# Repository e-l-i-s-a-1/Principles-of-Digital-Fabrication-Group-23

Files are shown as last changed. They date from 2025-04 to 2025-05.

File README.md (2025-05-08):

# Principles-of-Digital-Fabrication
## Group 23
### Violent light-chasing alarm clock

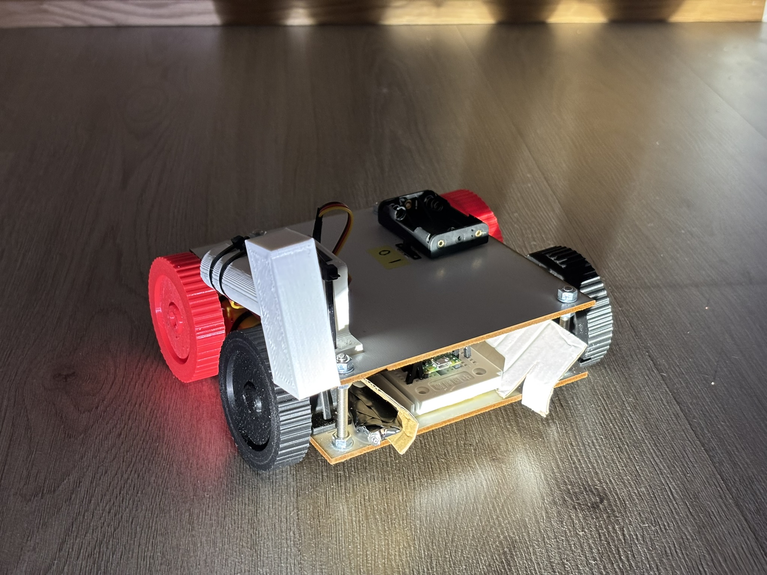
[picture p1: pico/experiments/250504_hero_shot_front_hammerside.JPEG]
Violent light-chasing alarm clock


---

### Contents of the repository:

```
cad:
    -stl-files of the 3D-printed components

pico:
    dev:
        -collection of Python-scripts tested with Pico (including the final "main_final.py")
        -final code with some comments as a .png
        -micropython firmware for Pico (.uf2)
        -schematic as a pptx- and jpeg-file
  
    docs:
        -documentations and datasheets of the used components
  
    experiments:
        -pictures and videos of the design/building process and testing

sketches:
    -some sketches and ideation from early phase of the design

-materials.xlsx (the materials & components list including costs and specifications)

-README.md (this file)
```

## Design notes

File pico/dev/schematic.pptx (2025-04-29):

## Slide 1

Battery holder (3 x AAA)

8 male-female jumpers
4 male-male jumper

ON

Switch

OFF

+

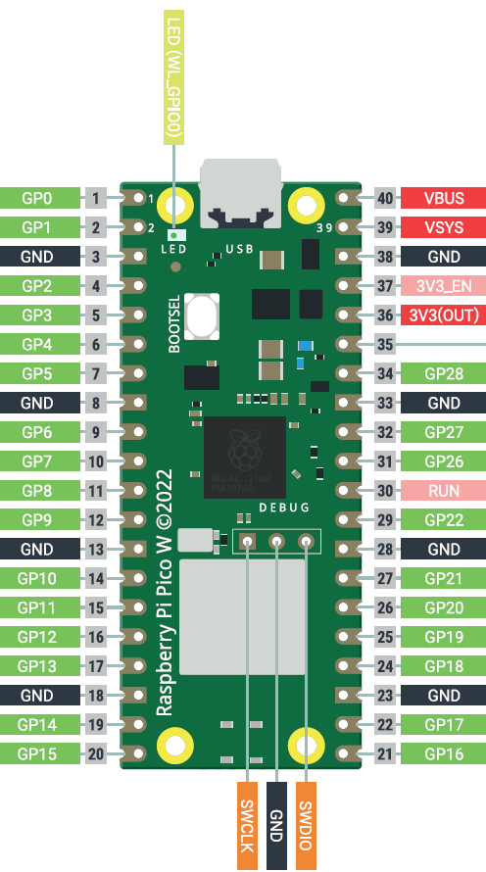
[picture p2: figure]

Big breadboard +

+

Big breadboard -

Schottky diode

C

C

Phototransistor L

E

E

Motor R signal

Phototransistor R

10kΩ resistor

Motor L signal

10kΩ resistor

Servo signal

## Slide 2

Motor R

+

Big breadboard +

Servo

PWM

+

Big breadboard -

Motor R signal

Big breadboard +

O4

L293D H-bridge

VSS

I4

G

G

O3

I3

E2

Big breadboard -

Big breadboard +

Servo signal

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
Motor L signal

3 male-male jumpers

Big breadboard +

Big breadboard -

Big breadboard +

Motor L

+

12 male-male jumpers

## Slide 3

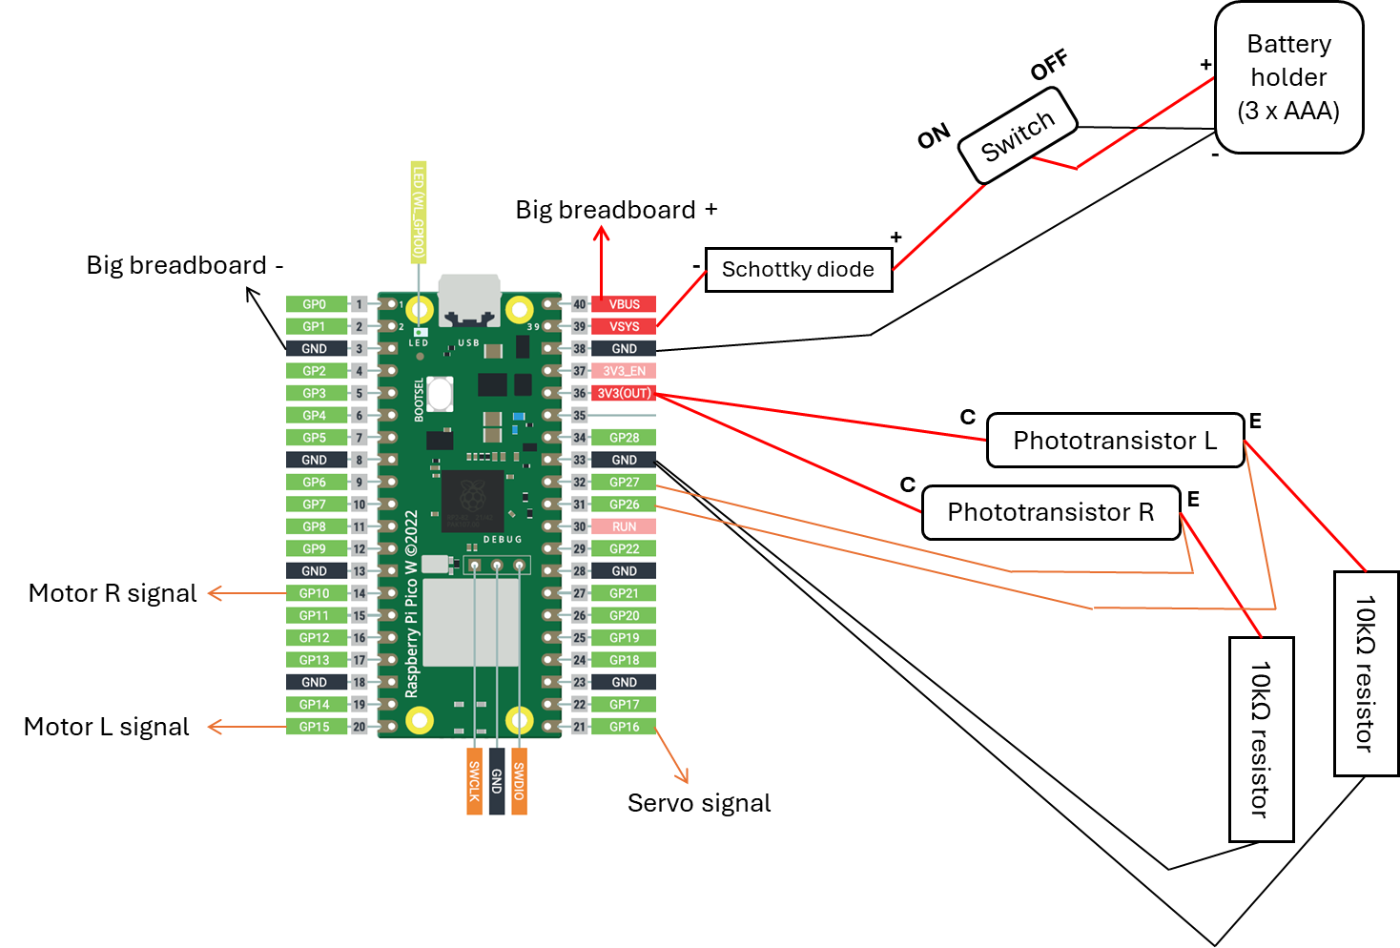
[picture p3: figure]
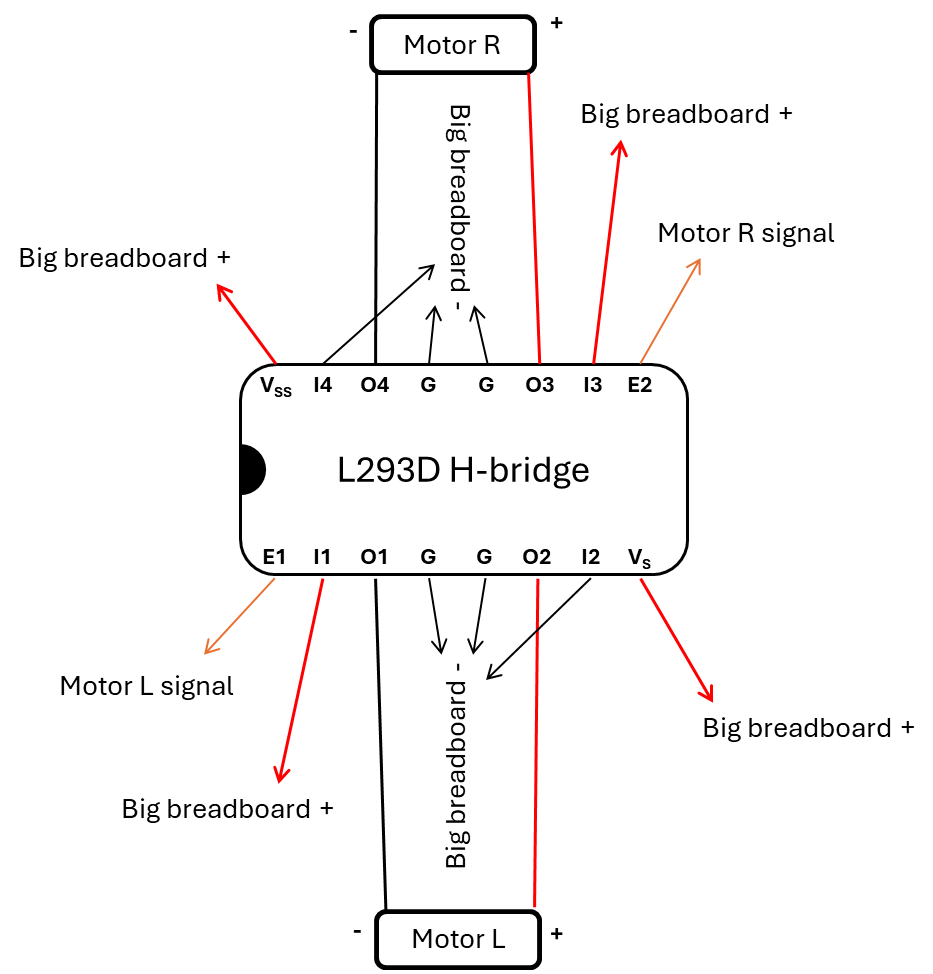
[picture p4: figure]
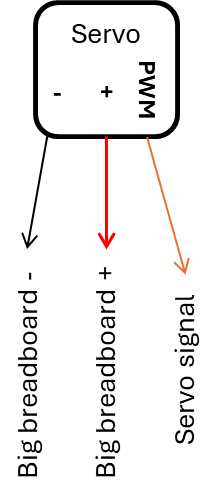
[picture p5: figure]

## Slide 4

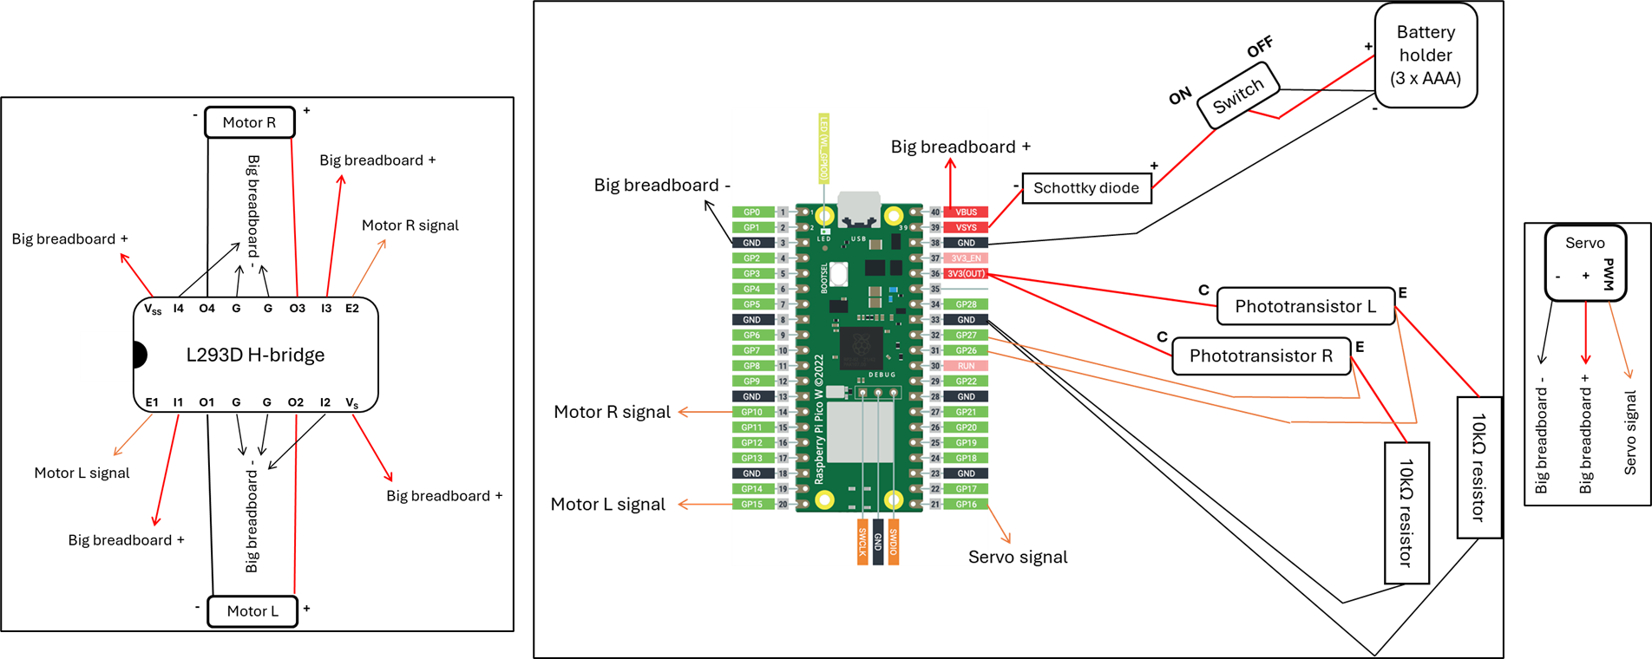
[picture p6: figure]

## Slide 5

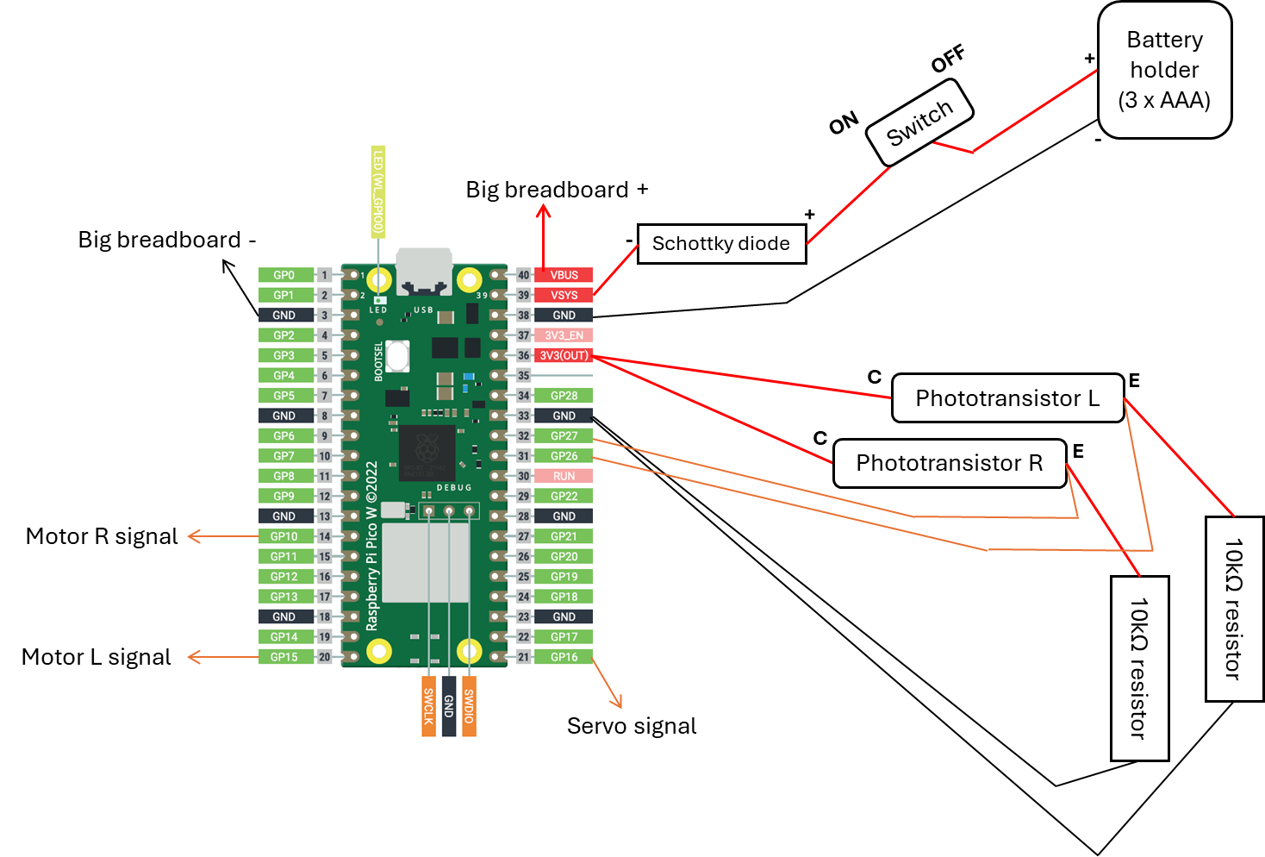
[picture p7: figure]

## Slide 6

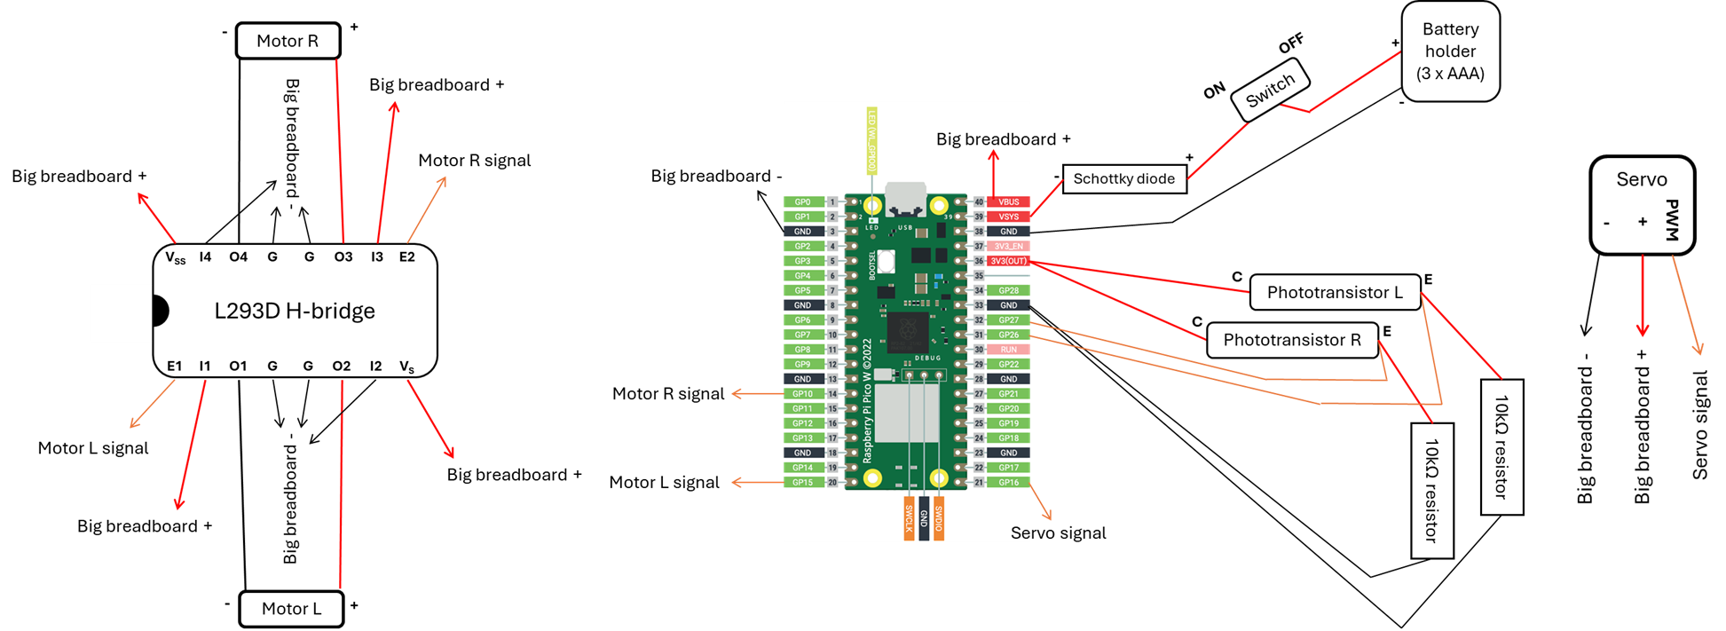
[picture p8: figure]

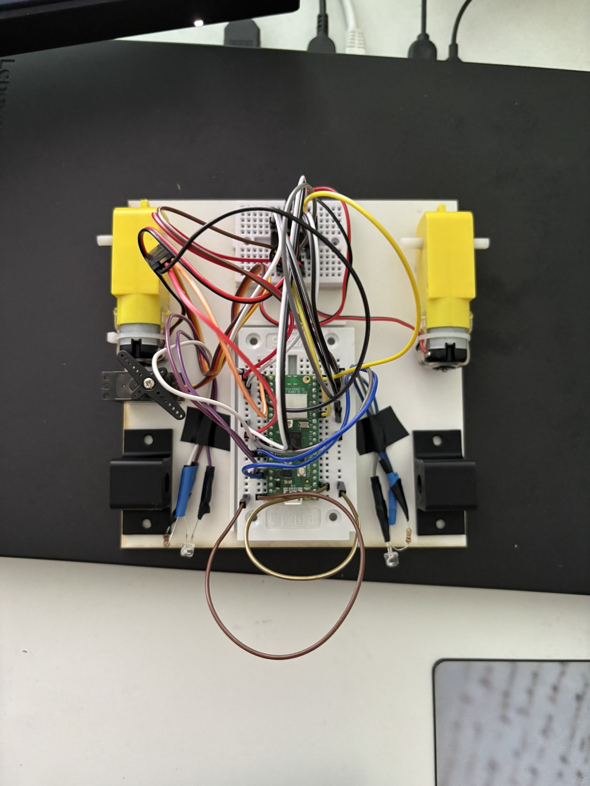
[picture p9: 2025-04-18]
pico/experiments/250417_electronics_topview.JPEG

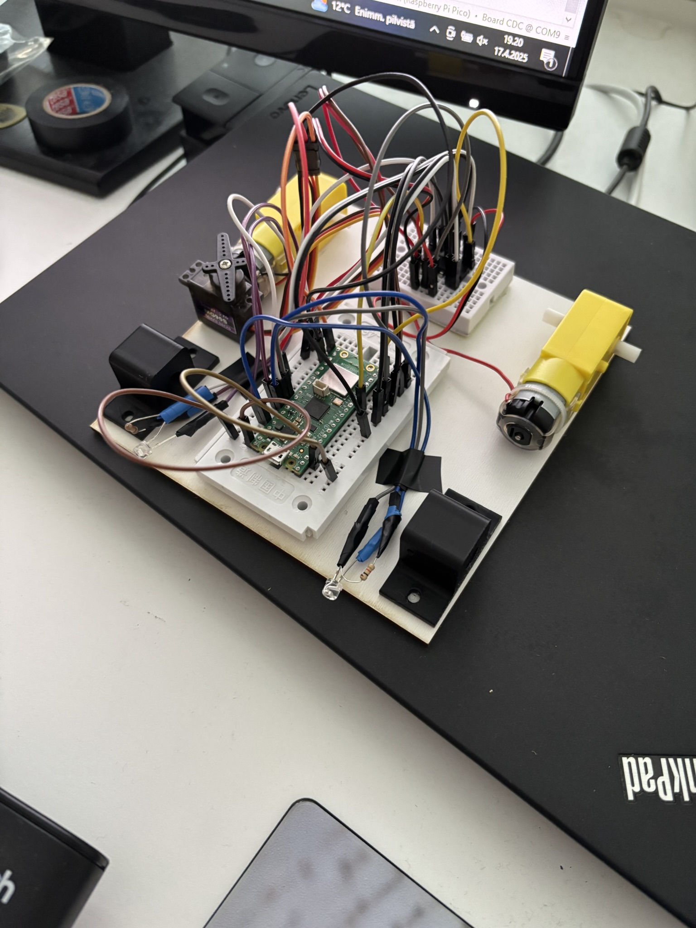
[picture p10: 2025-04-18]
pico/experiments/250417_electronics.JPEG

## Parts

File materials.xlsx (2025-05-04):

Materials
Group 23
violent light-chasing alarm clock |  |  | Updated: | 250503
# | Item | Size (in materials) | Quantity | Material / component specification | Cost per unit [€] | Unit | Total [€]
1 | Frame plate v1 | 135 x 65 x 3 mm | 4 | Plywood (thickness = 3 mm) | 2.1e-05 | mm2 | 0.7371
2 | Frame plate v2 | 150 x 145 x 3 mm | 2 | Plywood (thickness = 3 mm) | 2.1e-05 | mm2 | 0.9135
3 | Front wheel | 35931.574 mm3 / 28 g | 2 | PLA | 0.014 | g | 0.784
4 | Front wheel bracket v1 | 9213.417 mm3 / 9 g | 1 | PLA | 0.014 | g | 0.126
5 | Front wheel bracket v2 | 9002.649 mm3 / 9 g | 2 | PLA | 0.014 | g | 0.252
6 | Microcontroller |  | 1 | Raspberry Pi Pico W | 8.11 | piece | 8.11
7 | Breadboard |  | 1 | Big | 5.35 | piece | 5.35
8 | Breadboard |  | 1 | Small | 2.72 | piece | 2.72
9 | Phototransistor |  | 2 | TEPT5700 | 0.46 | piece | 0.92
10 | Resistor |  | 2 | 10k ohm | 0.24 | piece | 0.48
11 | Gear motor |  | 2 | GEARMOTOR 200 RPM 3-6V DC (Adafruit 3777) | 2.72 | piece | 5.44
12 | H-bridge |  | 1 | L293D | 7.24 | piece | 7.24
13 | Microservo |  | 1 | MG90S | 2.4 | piece | 2.4
14 | Jumper cable |  | 19 | Male-male | 0.1335 | piece | 2.5365
15 | Jumper cable |  | 8 | Male-female | 0.1315 | piece | 1.052
16 | Rear wheel |  | 2 | thin white wheel 65mm (Adafruit 3763) | 1.38 | piece | 2.76
17 | Schottky diode |  | 1 | STPS3L60 | 0.39 | piece | 0.39
18 | Slide switch |  | 1 | SPDT | 0.88 | piece | 0.88
19 | Battery holder |  | 1 | 3 x AAA | 1.67 | piece | 1.67
20 | Electrical tape |  |  |  | - | -
21 | Printed rear wheel | 34516.570 mm3 / 18 g | 2 | TPU | 0.049 | g | 1.764
22 | Servo bracket | 30372.943 mm3 / 21 g | 1 | PLA | 0.014 | g | 0.294
23 | Hammer | 45181.519 mm3 / 28 g | 1 | PLA | 0.014 | g | 0.392
24 | Prototype frame |  | 1 | Cardboard from recycling bin | - | -
25 | Prototype wheels |  | 2 | 0.33l recyclable soda cans | - | -
26 | Bolt |  | 4 | M5 x 50 mm | 0.099 | piece | 0.396
27 | Nut |  | 12 | M5 | 0.1196 | piece | 1.4352
28 | (Screw) |  | ?? | ?? |  | piece
29 | Cable tie |  |  |  | - | -
30 | Steel wire |  |  |  | - | -
31 | Washer |  | 16 | M5 | 0.1196 | piece | 1.9136
32 | Two-sided tape |  |  |  | - | -
33
34
35
36
37
38
39
40
 |  |  |  |  |  | TOTAL | 50.9559
 | (brackets for not yet implemented/ready components/materials) |  |  |  |  | FINAL ASSEMBLY | 47.3328
 |  |  |  |  |  | -final assembly includes for example only the printed rear wheels

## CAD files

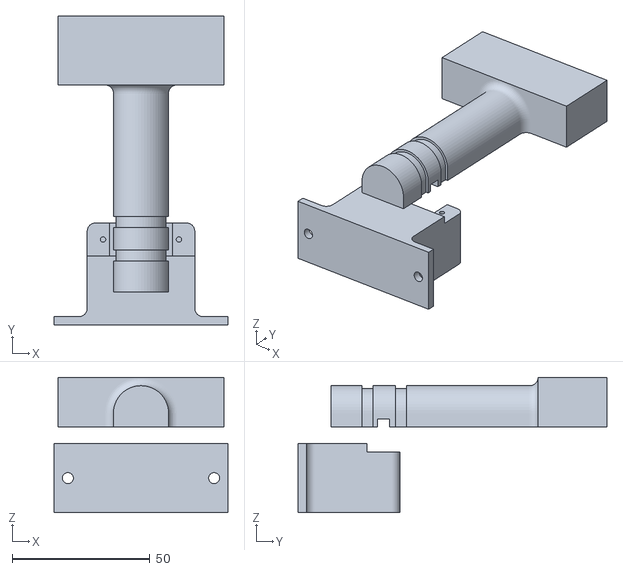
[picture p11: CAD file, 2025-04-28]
cad/hammer_assembly.stl
63.0 x 112.0 x 49.0

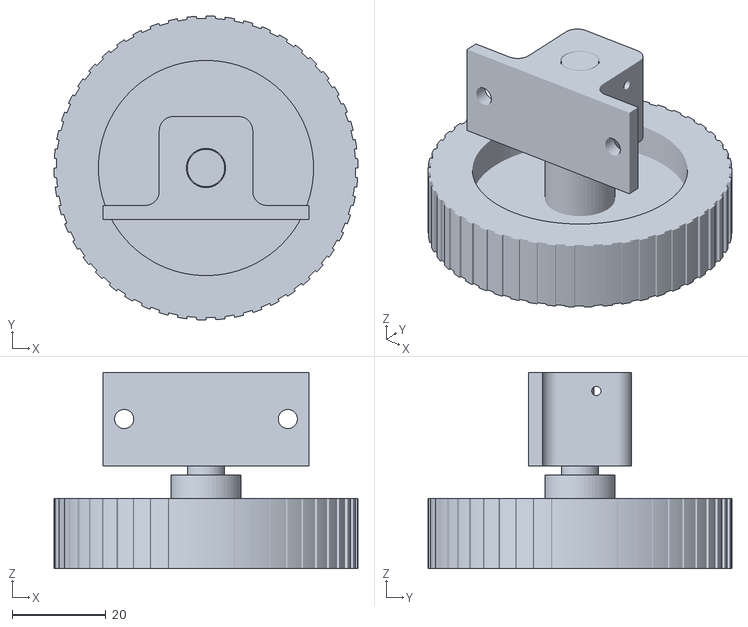
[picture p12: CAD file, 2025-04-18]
cad/wheel_front_assembly_v2.stl
65.0 x 65.0 x 42.0

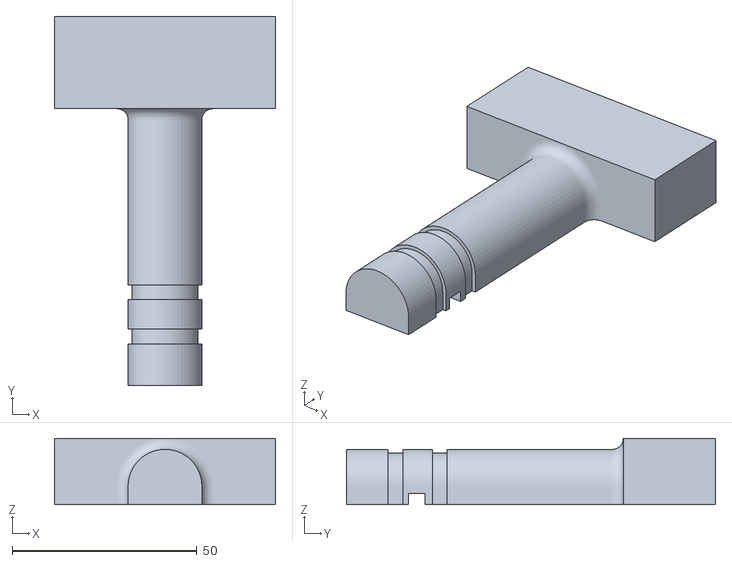
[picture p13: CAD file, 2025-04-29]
cad/hammer.stl
60.0 x 100.0 x 18.0

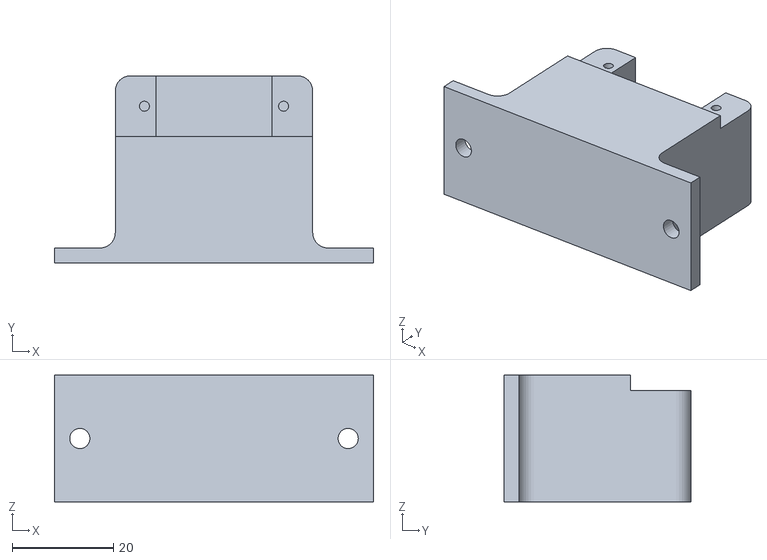
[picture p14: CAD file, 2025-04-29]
cad/servo_bracket.stl
63.0 x 37.0 x 25.0

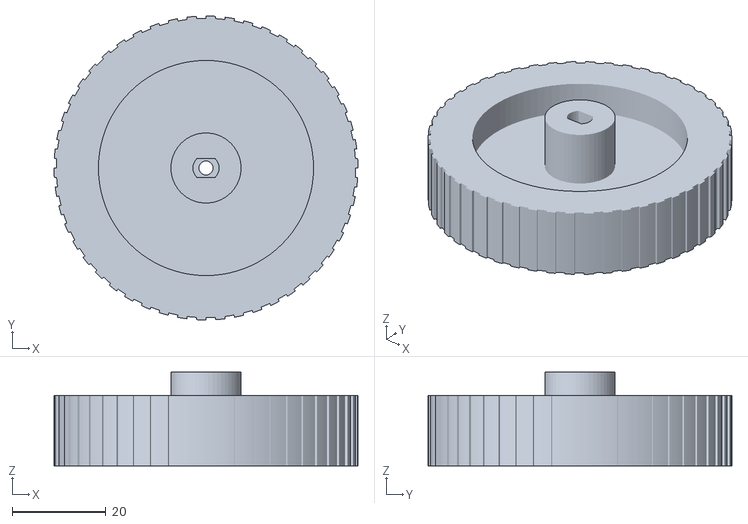
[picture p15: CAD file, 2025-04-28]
cad/wheel_rear.stl
65.0 x 65.0 x 20.0

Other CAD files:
cad/wheel_front_assembly.stl

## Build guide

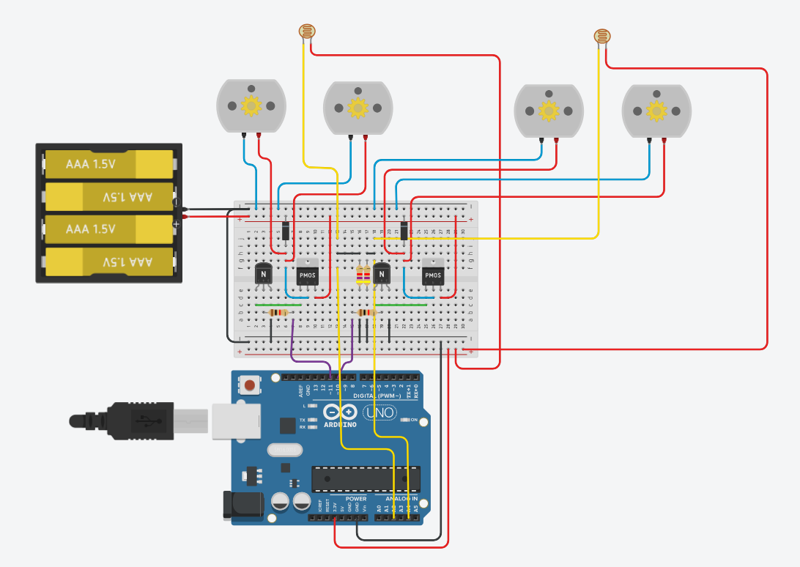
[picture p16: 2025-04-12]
sketches/first_tinkercad_assembly.png

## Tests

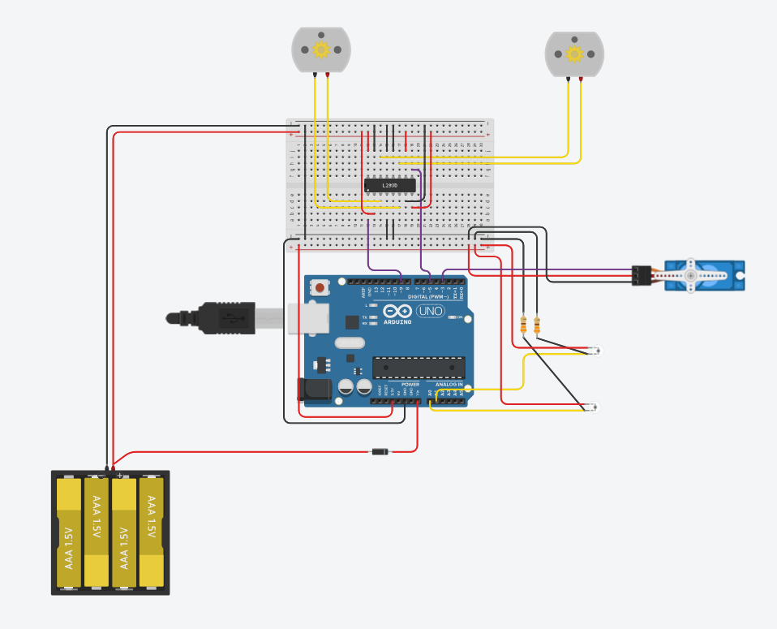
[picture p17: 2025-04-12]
pico/experiments/250406_tinkercad.png

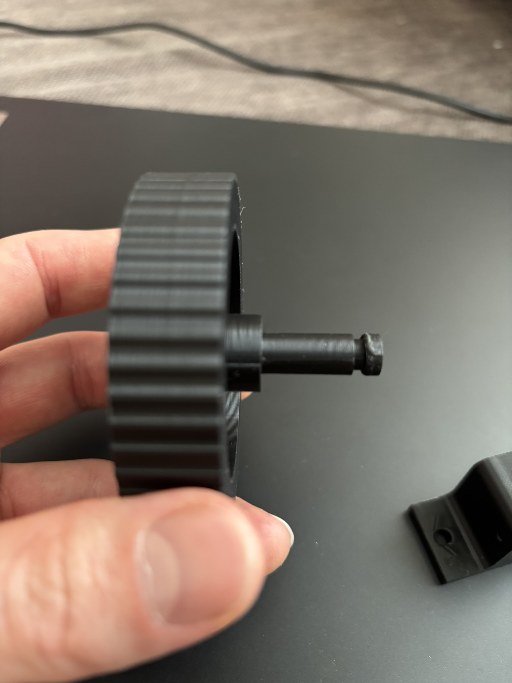
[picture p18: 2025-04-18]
pico/experiments/250417_wheel_groove.JPEG

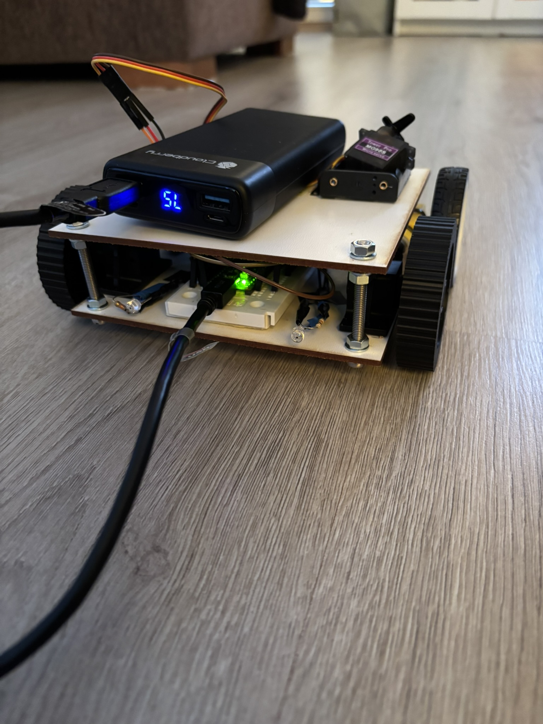
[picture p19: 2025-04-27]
pico/experiments/250427_first_test2.JPEG

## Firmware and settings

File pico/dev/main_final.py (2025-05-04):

from machine import Pin, ADC, PWM
from servo import Servo
import utime

# !!! save as main.py to pico !!!

utime.sleep(1)

debug = False # boolean for debug prints

led = Pin("LED", Pin.OUT) # built-in led to indicate power ON & READY

min_max_value = (0, 65535) # pico uint16 range
sample_delay = 0.1 # delay between cycles [s] # TUNING PARAMETER

### phototransistor setup
sensor_L = ADC(26) # A0 (left sensor)
sensor_R = ADC(27) # A1 (right sensor)
# checking the ambient light level and setting the light threshold
print("Sensing the illuminance level of the current surroundings...")
light_values = []
for i in range(5):
    light_L = sensor_L.read_u16()
    light_R = sensor_R.read_u16()
    light_values.append((light_L + light_R) / 2)
    utime.sleep(sample_delay * 2)
threshold = sum(light_values) / len(light_values)
init_threshold_factor = 1.5 # TUNING PARAMETER
threshold = int(init_threshold_factor * threshold)
init_threshold = threshold # save the initial threshold
print("initial threshold: %d" % threshold)

### motors setup
motor_L = PWM(Pin(15))
motor_R = PWM(Pin(10))
motor_L.freq(50) # [Hz]
motor_R.freq(50) # [Hz]
# minimum value for motor speed (45680 to get the minimum 2.3V)
speed_transfer = 55000 # TUNING PARAMETER
# scale factor for scaling light values to motor speed
speed_factor = round((min_max_value[1] - speed_transfer) / min_max_value[1], 2)
# check limits (speed factor = [0.0, 1.0])
speed_factor = max(0.0, speed_factor)
speed_factor = min(1.0, speed_factor)
print("speed_factor: %.2f" % speed_factor)
print("-> speed range: %d - %d" % (int(speed_transfer + speed_factor * min_max_value[0]),
                                   min(int(speed_transfer + speed_factor * min_max_value[1]), min_max_value[1])))

### servo setup (with micropython-servo package)
## defaults: Servo(min_us=544.0, max_us=2400.0 ,min_deg=0.0, max_deg=180.0, freq=50)
servo = Servo(pin_id=16, min_us=1000.0, max_us=2000.0, min_deg=-90.0, max_deg=90.0, freq=50)
min_max_degs = (-70.0, 70.0) # rotation range [deg] # TUNING PARAMETER
servo_inc = 3 # rotation increment [deg] # TUNING PARAMETER
servo_delay = 0.005 # delay between rotation increments [s] # TUNING PARAMETER
servo.write(min_max_degs[0]) # initial position min rotation

utime.sleep(1)

led.value(True) # led ON

try:
    while True:
        i = servo.read() # returns the last set degs
        
        # read light level on bot sides
        light_L = sensor_L.read_u16()
        light_R = sensor_R.read_u16()
        if debug:
            print("light_L = %d" % light_L)
            print("light_R = %d" % light_R)
        
        # update running average of the light level
        tmp_light_values = light_values[:-1]
        light_values = [(light_L + light_R) / 2]
        light_values.extend(tmp_light_values)
        light_value = int(sum(light_values) / len(light_values))
        
        # modify threshold if current conditions (running average) have changed enough
        if abs(light_value - threshold) > 2000:
            threshold = max(light_value, init_threshold)
            if debug:
                print("threshold changed to: %d" % threshold)
        
        # run motors if light level is over current threshold
        if light_L >= threshold:
            motor_R_speed = int(speed_transfer + speed_factor * light_L)
            motor_R.duty_u16(min(motor_R_speed, min_max_value[1]))
        else:
            motor_R.duty_u16(0)
        if light_R >= threshold:
            motor_L_speed = int(speed_transfer + speed_factor * light_R)
            motor_L.duty_u16(min(motor_L_speed, min_max_value[1]))
        else:
            motor_L.duty_u16(0)
        
        # swing hammer if light level is over initial threshold
        max_light = max(light_L, light_R)
        if max_light >= init_threshold:
            while i < min_max_degs[1]: # rotates servo +increment at a time until max rotation
                i += servo_inc
                servo.write(i)
                utime.sleep(servo_delay)
            while i > min_max_degs[0]: # rotates servo -increment at a time until min rotation
                i -= servo_inc
                servo.write(i)
                utime.sleep(servo_delay)
        else:
            if i != min_max_degs[0]:
                servo.write(min_max_degs[0])

        # short pause before the next cycle
        utime.sleep(sample_delay)
        
except KeyboardInterrupt:
    print("Stopping the program")
    led.value(False) # led OFF
    servo.write(min_max_degs[0]) # finally min rotation
    motor_L.duty_u16(0) # stop motors
    motor_R.duty_u16(0)
    utime.sleep(1)

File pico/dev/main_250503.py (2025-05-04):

from machine import Pin, ADC, PWM
from servo import Servo
import utime

utime.sleep(1)

prints = False # boolean for prints

led = Pin("LED", Pin.OUT) # built-in led to indicate power ON

print("TESTING NEW VERSION")

min_max_value = (0, 65535) # pico u16 range
sample_delay = 0.15 # delay for tuning overall response [s]

### phototransistor setup
sensor_L = ADC(26) # A0 (left sensor)
sensor_R = ADC(27) # A1 (right sensor)
print("Sensing the illuminance level of the current surroundings...")
light_values = []
for i in range(10):
    light_L = sensor_L.read_u16()
    light_R = sensor_R.read_u16()
    light_values.append((light_L + light_R) / 2)
    utime.sleep(sample_delay * 2)
light_value = int(sum(light_values) / len(light_values))
th_value = light_value / (min_max_value[1] - min_max_value[0])
th_value = th_value + th_value * 0.5
th_value = round(th_value, 4)
print("th_value: %.4f" % th_value)
del light_values
del light_value
d_tuning = int((min_max_value[1] - min_max_value[0]) * 0.01)

# checking accepted limits
# scaling threshold to u16
if th_value > 1.0:
    th_value = 1.0
elif th_value < 0.0:
    th_value = 0.0
threshold = int(th_value * (min_max_value[1] - min_max_value[0]))
print("threshold: %d" % threshold)
del th_value

### motors setup
motor_L = PWM(Pin(15))
motor_R = PWM(Pin(10))
motor_L.freq(50) # [Hz]
motor_R.freq(50) # [Hz]
min_speed = 45680
motor_L_speed = min_speed
motor_R_speed = min_speed
speed_tuning = 5000
speed_factor = 0.8 # scale factor for motor speed tuning [0.0, 1.0]

# checking accepted limits
if speed_factor > 1.0:
    speed_factor = 1.0
elif speed_factor < 0.0:
    speed_factor = 0.0

### servo setup (with micropython-servo package)
## defaults: Servo(min_us=544.0, max_us=2400.0 ,min_deg=0.0, max_deg=180.0, freq=50)
servo = Servo(pin_id=16, min_us=1000.0, max_us=2000.0, min_deg=-90.0, max_deg=90.0, freq=50)
min_max_degs = (-70.0, 70.0) # rotation range [deg]
servo_delay = 0.005 # delay between 3deg rotation [s]
servo.write(min_max_degs[0]) # initial position min rotation

utime.sleep(1)

led.value(True)

try:
    while True:
        i = servo.read() # returns the last set degs
        prev_light_L = light_L # light values from previous cycle
        prev_light_R = light_R
        light_L = sensor_L.read_u16() # light values from current cycle
        light_R = sensor_R.read_u16()
        if prints:
            print("light_L = %d" % light_L)
            print("light_R = %d" % light_R)
        max_light = max(light_L, light_R)
        
        ### new test
        if max_light >= threshold:
            d_light_L = light_L - prev_light_L
            d_light_R = light_R - prev_light_R
            
            # control the right motor
            if d_light_L >= d_tuning:
                motor_R_speed += speed_tuning
                if motor_R_speed > min_max_value[1]:
                    motor_R_speed = min_max_value[1]
                motor_R.duty_u16(motor_R_speed)
            elif d_light_L < -d_tuning:
                motor_R_speed -= speed_tuning
                if motor_R_speed < min_speed:
                    motor_R_speed = min_speed
                motor_R.duty_u16(motor_R_speed)
            else:
                motor_R.duty_u16(0)
            
            # control the left motor
            if d_light_R >= d_tuning:
                motor_L_speed += speed_tuning
                if motor_L_speed > min_max_value[1]:
                    motor_L_speed = min_max_value[1]
                motor_L.duty_u16(motor_L_speed)
            elif d_light_R < -d_tuning:
                motor_L_speed -= speed_tuning
                if motor_L_speed < min_speed:
                    motor_L_speed = min_speed
                motor_L.duty_u16(motor_L_speed)
            else:
                motor_L.duty_u16(0)
            
            # control the servo
            while i < min_max_degs[1]: # rotates servo +3deg at a time until max rotation
                i += 3
                servo.write(i)
                utime.sleep(servo_delay)
            while i > min_max_degs[0]: # rotates servo -3deg at a time until min rotation
                i -= 3
                servo.write(i)
                utime.sleep(servo_delay)
        
        else:
            if i != min_max_degs[0]:
                servo.write(min_max_degs[0])
            motor_L.duty_u16(0)
            motor_R.duty_u16(0)
        utime.sleep(sample_delay)
        
#         # OLD
#         if max_light >= threshold:
#             if light_L >= threshold:
#                 motor_R.duty_u16(int(speed_factor * light_L))
#             else:
#                 motor_R.duty_u16(0)
#             if light_R >= threshold:
#                 motor_L.duty_u16(int(speed_factor * light_R))
#             else:
#                 motor_L.duty_u16(0)
#             while i < min_max_degs[1]: # rotates servo +3deg at a time until max rotation
#                 i += 3
#                 servo.write(i)
#                 utime.sleep(servo_delay)
#             while i > min_max_degs[0]: # rotates servo -3deg at a time until min rotation
#                 i -= 3
#                 servo.write(i)
#                 utime.sleep(servo_delay)
#         else:
#             if i != min_max_degs[0]:
#                 servo.write(min_max_degs[0])
#             motor_L.duty_u16(0)
#             motor_R.duty_u16(0)
#         utime.sleep(sample_delay)
        
except KeyboardInterrupt:
    if prints:
        print("Stopping the program")
    led.value(False)
    servo.write(min_max_degs[0]) # finally min rotation
    motor_L.duty_u16(0)
    motor_R.duty_u16(0)
    utime.sleep(1)

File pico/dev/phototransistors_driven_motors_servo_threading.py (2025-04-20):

from machine import Pin, ADC, PWM
from servo import Servo
import utime
import _thread

utime.sleep(1)

class Shared:
    min_max_value = (0, 65535) # pico u16 range
    sample_delay = 0.25 # delay for tuning overall response [s]
    
    ### servo setup (with micropython-servo package)
    ## defaults: Servo(min_us=544.0, max_us=2400.0 ,min_deg=0.0, max_deg=180.0, freq=50)
    servo = Servo(pin_id=16, min_us=1000.0, max_us=2000.0, min_deg=-90.0, max_deg=90.0, freq=50)
    min_max_degs = (-80.0, 80.0) # rotation range [deg]
    servo_delay = 0.005 # delay between 5deg rotation [s]
    servo.write(min_max_degs[0]) # initial position min rotation
    
    ### phototransistor setup
    sensor_L = ADC(26) # A0 (left sensor)
    sensor_R = ADC(27) # A1 (right sensor)
    th_value = 0.6 # threshold value [0.0, 1.0] for sensitivity
    # checking accepted limits
    if th_value > 1.0:
        th_value = 1.0
    elif th_value < 0.0:
        th_value = 0.0
    # scaling threshold to u16
    threshold = int(th_value * (min_max_value[1] - min_max_value[0]))
    
    @classmethod
    def read_sensor_L(cls):
        # reads the u16 value from the left phototransistor
        return cls.sensor_L.read_u16()
    
    @classmethod
    def read_sensor_R(cls):
        # reads the u16 value from the right phototransistor
        return cls.sensor_R.read_u16()
    
    @classmethod
    def read_servo(cls):
        # returns the last set degs from the servo
        return cls.servo.read()
    
    @classmethod
    def write_servo(cls, deg):
        # sets degrees to servo
        cls.servo.write(deg)

def servo_thread():
    try:
        while True:
            # if enough light is sensed at any sensor, the servo rotates once back and forth
            light_L = Shared.read_sensor_L()
            light_R = Shared.read_sensor_R()
            print("light_L = %d" % light_L)
            print("light_R = %d" % light_R)
            max_light = max(light_L, light_R)
            if max_light >= Shared.threshold:
                i = Shared.read_servo()
                while i < Shared.min_max_degs[1]: # rotates servo +5deg at a time until max rotation
                    i += 5
                    Shared.write_servo(i)
                    utime.sleep(Shared.servo_delay)
                while i > Shared.min_max_degs[0]: # rotates servo -5deg at a time until min rotation
                    i -= 5
                    Shared.write_servo(i)
                    utime.sleep(Shared.servo_delay)
            utime.sleep(Shared.sample_delay)
    
    except KeyboardInterrupt:
        print("Stopping the program")
        Shared.write_servo(Shared.min_max_degs[0]) # finally min rotation
        utime.sleep(1)

def motor_thread(motor_L, motor_R, speed_factor):
    try:
        while True:
            # if enough light sensed at left sensor, right motor rotates (and vice versa)
            # motor speed is based on the intensity of the light
            light_L = Shared.read_sensor_L()
            light_R = Shared.read_sensor_R()
            if light_L >= Shared.threshold:
                motor_R.duty_u16(int(speed_factor * light_L))
            else:
                motor_R.duty_u16(0)
            if light_R >= Shared.threshold:
                motor_L.duty_u16(int(speed_factor * light_R))
            else:
                motor_L.duty_u16(0)
            utime.sleep(Shared.sample_delay)
            
    except KeyboardInterrupt:
        motor_L.duty_u16(0)
        motor_R.duty_u16(0)
        utime.sleep(1)

### motors setup
motor_L = PWM(Pin(15))
motor_R = PWM(Pin(10))
motor_L.freq(50) # [Hz]
motor_R.freq(50) # [Hz]
speed_factor = 0.5 # scale factor for motor speed tuning [0.0, 1.0]
# checking accepted limits
if speed_factor > 1.0:
    speed_factor = 1.0
elif speed_factor < 0.0:
    speed_factor = 0.0

utime.sleep(1)

Shared.write_servo(Shared.min_max_degs[0])

### start servo thread on core 1
core1_thread = _thread.start_new_thread(servo_thread, ())

### main thread on core 0
motor_thread(motor_L, motor_R, speed_factor)

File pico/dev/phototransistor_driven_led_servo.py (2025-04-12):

from machine import Pin, ADC
from servo import Servo
import utime

utime.sleep(1)

### pico ADC range
min_max_value = (0, 65535)

### phototransistor setup
sensor = ADC(26) # A0
threshold = int(0.6 * (min_max_value[1] - min_max_value[0]))

### led setup
led = Pin(5, Pin.OUT)
led.low() # initially OFF

### servo setup (with micropython-servo package)
## defaults: Servo(min_us=544.0, max_us=2400.0 ,min_deg=0.0, max_deg=180.0, freq=50)
servo = Servo(pin_id=16, min_us=1000.0, max_us=2000.0, min_deg=-90.0, max_deg=90.0, freq=50)
min_max_degs = (-80.0, 80.0) # rotation range
delay = 0.005 # s
servo.write(min_max_degs[0]) # initial position min rotation

utime.sleep(1)

try:
    while True:
        light = sensor.read_u16()
        print("light = %d" % light)
        if light > threshold:
            print("things happen")
            led.high() # led ON
            i = servo.read() # returns the last set degs
            while i < min_max_degs[1]: # rotates servo +1deg at a time until max rotation
                i += 5
                servo.write(i)
                utime.sleep(delay)
            utime.sleep(0.5)
            while i > min_max_degs[0]: # rotates servo -1deg at a time until min rotation
                i -= 5
                servo.write(i)
                utime.sleep(delay)
        else:
            led.low() # led OFF
            servo.write(min_max_degs[0])
        utime.sleep(0.5)
        
except KeyboardInterrupt:
    print("Stopping the program")
    led.low() # finally OFF
    servo.write(min_max_degs[0]) # finally min rotation
    utime.sleep(1)

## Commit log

2025-04-12 added some pico experiment codes, pics and docs + frame idea sketches
2025-04-12 updated /pico/dev/phototransistor_driven_led_servo.py (tested succesfully)
2025-04-16 added first drafts of the final code and schematic
2025-04-16 added a threaded version of the gadget code
2025-04-18 added materials.xlsx, front wheel assembly stl-files & new process pictures. updated gadget schematic & sequential gadget code (tested as functional with all the actuators & sensors)
    [materials.xlsx, wheel_front_assembly.stl, wheel_front_assembly_v2.stl]
2025-04-20 updated materials.xlsx, schematic.pptx & multithreaded code (might not be needed though, the single core code worked better than expected). added datasheet for gearbox motor.
    [materials.xlsx]
2025-04-23 updated materials.xlsx with draft costs
    [materials.xlsx]
2025-04-27 added pics from first full assembly and main.py that works with external power source (without laptop). updated materials list.
    [materials.xlsx]
2025-04-28 added stl-files for rear wheel and hammer assembly
    [hammer_assembly.stl, wheel_rear.stl]
2025-04-29 added hammer and servo bracket as separate stl-files also
    [hammer.stl, servo_bracket.stl]
2025-04-29 updated materials list and schematic
    [materials.xlsx]
2025-05-04 updated materials list & readme-file. added pics and demo video from final testing session & several versions of the final code (main_final.py is the one saved into the pico)
    [materials.xlsx]
